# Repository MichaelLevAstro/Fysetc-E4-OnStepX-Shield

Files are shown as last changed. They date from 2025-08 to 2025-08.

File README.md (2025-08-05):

# Shield for adding Extra modules to FYSETC E4 Board



## Added features
- GPS through X-Min pin
- MCP23017 IO expander for homing sensors using I2C
- FRAM for persistent data
- 5V Laser with Switch
- 12v to 24v step up module for a Motor Brake using an XL6009 module

Links to modules:
FRAM:
https://www.aliexpress.com/item/1005006584211412.html?sk=6mia6uv

MCP23017:
https://www.aliexpress.com/item/1005005335661057.html?spm=a2g0o.order_list.order_list_main.26.48951802nkMEFA

DC Step up:
https://www.aliexpress.com/item/32762092828.html?spm=a2g0o.order_list.order_list_main.37.48951802nkMEFA

Home sensors i used (Wide body):
https://www.aliexpress.com/item/32990256417.html?spm=a2g0o.order_list.order_list_main.58.48951802nkMEFA

GPS:
https://www.aliexpress.com/item/1005006495592091.html?spm=a2g0o.order_list.order_list_main.47.48951802nkMEFA
*note: any GPS using a TX should work (as long as it works with TinyGPS++)
*note2: GPS is very sensitive and often can communicate with enough satellites and cant get a fix, up to you to make it work properly in your enclosure.

Laser:
Any 5v laser should work fine

# OnStepX configurations
In config.h

```
#define LIMIT_SENSE_PIN                 0 // Set this to 0 or even comment it out, wont be used

// FRAM
#define NV_DRIVER             NV_MB85RC64

// Homing sensors
#define AXIS1_SENSE_HOME             HIGH
#define AXIS2_SENSE_HOME             HIGH

// GPS
#define TIME_LOCATION_SOURCE          GPS
#define SERIAL_GPS SoftSerial
#define SERIAL_GPS_RX 34
#define SERIAL_GPS_TX 0 // must be set or wont compile
#define SERIAL_GPS_BAUD 9600
```

In src\pinmaps\Pins.FYSETC_E4.h:
```
// Needed for IO expander to work
#define AXIS1_SENSE_HOME_PIN  GPIO_PIN(0)
#define AXIS2_SENSE_HOME_PIN   GPIO_PIN(1)
```

# Connections
E4ShieldConnections

*note: X-Min connector in the shield is a 2 pin connector, you dont have to connect GND, you can connect only the X-Min.

# Assembly
I used M3 standoffs, and removed anything tall from the board, the original heatsinks for the motors drivers and the green power connectors.
Had to make room to fit in my mount.
WhatsApp Image 2025-07-10 at 00 03 44_10ef709c

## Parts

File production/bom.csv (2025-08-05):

Designator | Footprint | Quantity | Value | LCSC Part #
BRAKE1 | JST_XH_B2B-XH-A_1x02_P2.50mm_Vertical | 1 | BRK
DC1 | XL6009E1 | 1 | ~
FRAM1 | FRAM_MB85RC256V | 1 | ~
GPS1 | JST_XH_B4B-XH-A_1x04_P2.50mm_Vertical | 1 | Conn_01x04
INPUT1 | JST_XH_B4B-XH-A_1x04_P2.50mm_Vertical | 1 | I2C_pwr
INPUT12V1 | JST_XH_B2B-XH-A_1x02_P2.50mm_Vertical | 1 | BRK_PWR_IN
LASER1, LASER_SW1 | JST_XH_B2B-XH-A_1x02_P2.50mm_Vertical | 2 | Conn_01x02
MCP1 | MCP23017_Module | 1 | ~
XMIN1 | JST_XH_B2B-XH-A_1x02_P2.50mm_Vertical | 1 | XMin
X_HM1 | JST_XH_B3B-XH-A_1x03_P2.50mm_Vertical | 1 | X_Home
Y_HM1 | JST_XH_B3B-XH-A_1x03_P2.50mm_Vertical | 1 | Y_Home

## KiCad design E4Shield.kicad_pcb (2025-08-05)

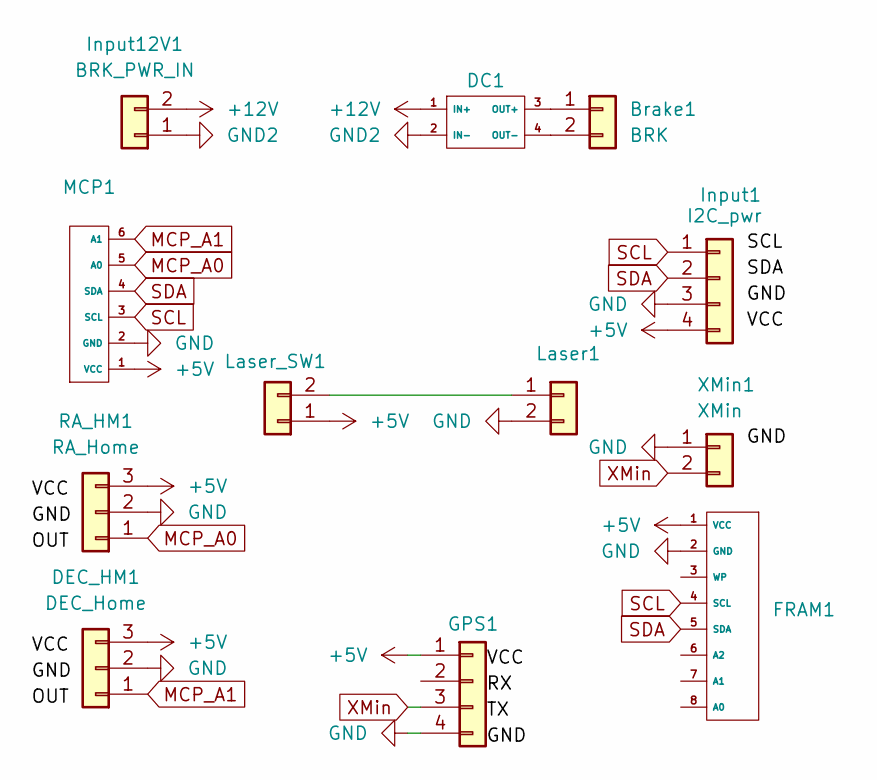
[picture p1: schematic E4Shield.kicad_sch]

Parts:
Brake1: BRK; JST_XH_B2B-XH-A_1x02_P2.50mm_Vertical
DC1: XL6009E1
DEC_HM1: DEC_Home; JST_XH_B3B-XH-A_1x03_P2.50mm_Vertical
FRAM1: FRAM_MB85RC256V
GPS1: Conn_01x04; JST_XH_B4B-XH-A_1x04_P2.50mm_Vertical
Input1: I2C_pwr; JST_XH_B4B-XH-A_1x04_P2.50mm_Vertical
Input12V1: BRK_PWR_IN; JST_XH_B2B-XH-A_1x02_P2.50mm_Vertical
Laser1: Conn_01x02; JST_XH_B2B-XH-A_1x02_P2.50mm_Vertical
Laser_SW1: Conn_01x02; JST_XH_B2B-XH-A_1x02_P2.50mm_Vertical
MCP1: MCP23017_Module
RA_HM1: RA_Home; JST_XH_B3B-XH-A_1x03_P2.50mm_Vertical
XMin1: XMin; JST_XH_B2B-XH-A_1x02_P2.50mm_Vertical

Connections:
+5V: DEC_HM1.3, FRAM1.1 (VCC), GPS1.1, Input1.4, Laser_SW1.1, MCP1.1 (VCC), RA_HM1.3
+12V: DC1.1 (IN+), Input12V1.2
GND: DEC_HM1.2, FRAM1.2 (GND), GPS1.4, Input1.3, Laser1.2, MCP1.2 (GND), RA_HM1.2, XMin1.1
GND2: DC1.2 (IN-), Input12V1.1
MCP_A0: MCP1.5 (A0), RA_HM1.1
MCP_A1: DEC_HM1.1, MCP1.6 (A1)
unnamed: Brake1.1, DC1.3 (OUT+)
unnamed: Brake1.2, DC1.4 (OUT-)
unnamed: Laser1.1, Laser_SW1.2
SCL: FRAM1.4 (SCL), Input1.1, MCP1.3 (SCL)
SDA: FRAM1.5 (SDA), Input1.2, MCP1.4 (SDA)
XMin: GPS1.3, XMin1.2

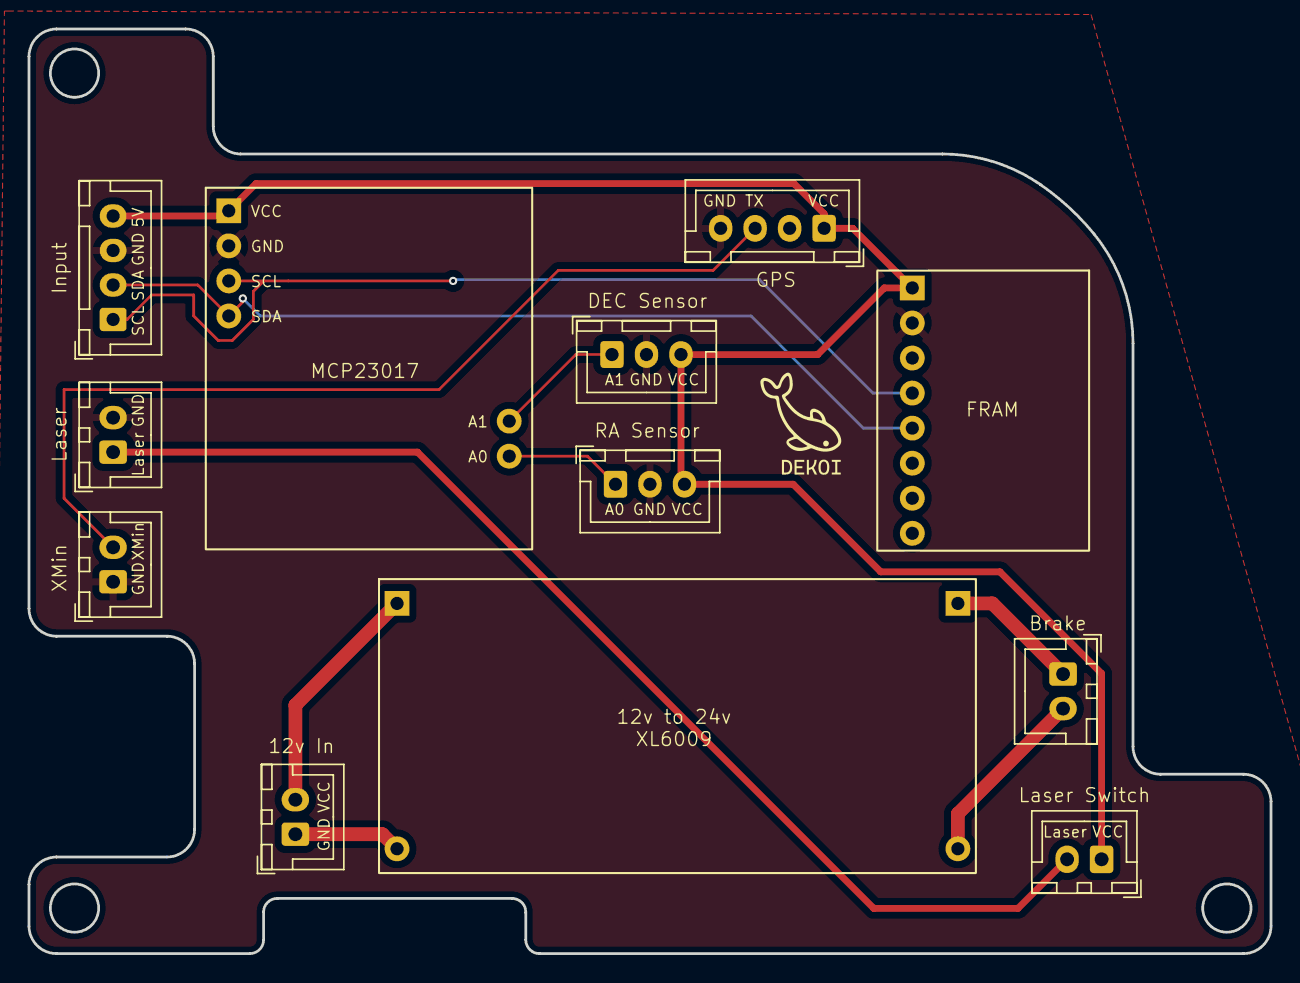
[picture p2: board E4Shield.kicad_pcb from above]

Board: 2 copper layers, 90.0 x 67.0 mm, 12 parts (0 on the bottom side), 12 nets.
